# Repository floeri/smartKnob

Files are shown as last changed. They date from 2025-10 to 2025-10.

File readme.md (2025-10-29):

# Modified SmartKnob code for the MaTouch

This is a modified fork of https://gitee.com/coll45/super-dial-motor-knob-screen for the hardware of the MaTouch SmartKnob https://www.makerfabs.com/matouch-smartknob-assembled.html using the ESP-IDF

### Attention: 
the Arduino code in this repo is not yet modified for the MaTouch hardware, only the IDF code.

## Demo Mode:
currently there is a demo-mode implemented showing different grid sizes. The knob parameters for this are hardcoded in idf_code/main/ui/screens/ui_Screnn3.c

On the device you can reach the demo mode by selecting custom HID in the main menu

## TODOs
- translate chinese comments
- integrate tiny-usb midi library
- implement basic midi CC funktions to be able to use it as a midi controller
- create a flexible knob class that allows easy changes of the knob parameters
- restructure userinterface, get rid of unused code
- a lot of general refactoring

# Original README from the parent repo:

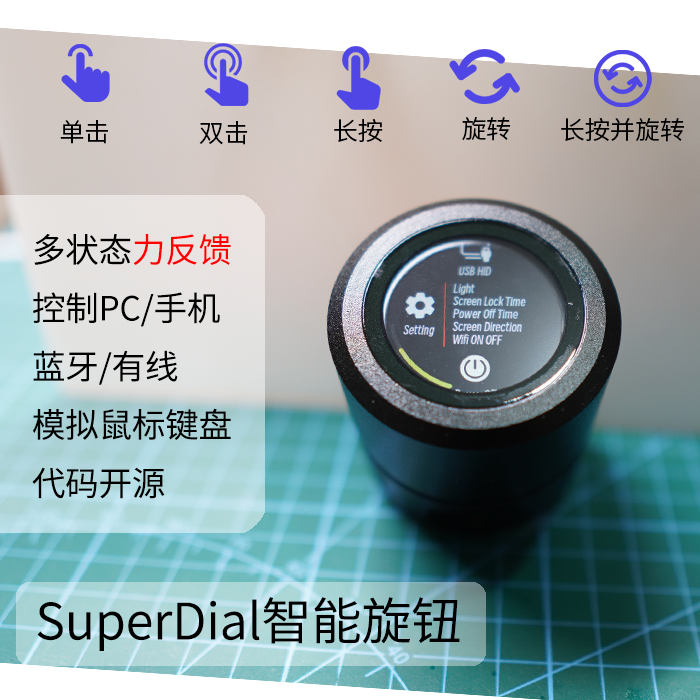
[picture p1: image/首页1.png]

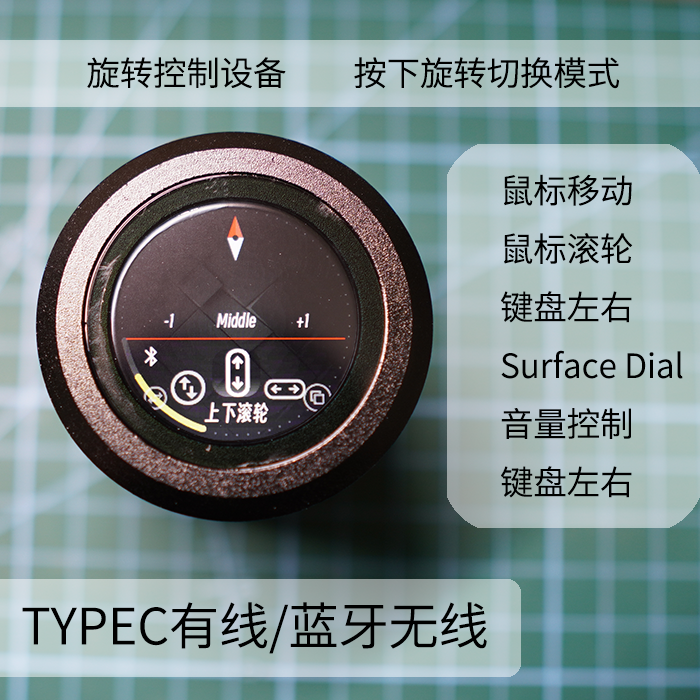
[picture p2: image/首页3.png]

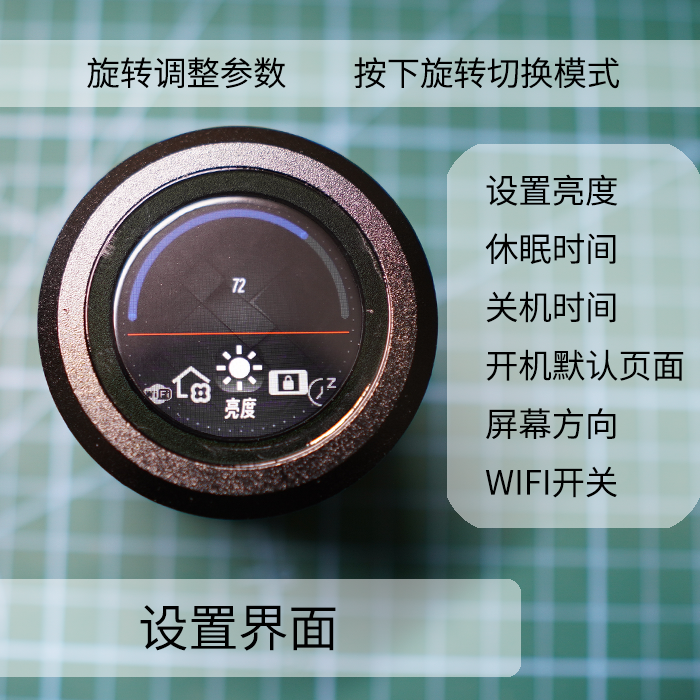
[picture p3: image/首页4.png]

# Super Dial 电机旋钮屏
##更新日志
### **重要更新2024/1/26:**
* **3205A电机已基本无货，需要改成3205B电机，修改内容如下**
  * 电机驱动板更改定位孔
  * 电机适配器修改为适配3205B
  * 电机转子套修改为适配3205B
  * 需要购买的螺丝变动具体查看3205B的bom表
### **重要更新2023/2/10:**

* **主控板V1更新为V2（打板 `不要打V1版本了）`，修复ip5306不稳定问题导致的电机转动时芯片重启、打开esp32wifi功能时供电不稳重启。 `删除USB引脚上的电容`（V1版本的C10、C11）让USB正常工作，原因是100nf电容太大了导致USB不能正常识别，去除电容就可以**
* **优化项：更换充电芯片使充电电流限制在400mA提高电池使用寿命，设计ups电路可实现USB和电池供电不间断切换，保证USB2.0也可以正常使用**
* **新的代码+固件也一并开源至Gitee**
* 硬件应该为最终版本，不再改动。代码会继续画饼（2024年注：电机坚持了一年才没货已经挺好了，所以硬件有小改动，换了几个螺丝孔位）

2022/10/10：原理图中usb5Vin 经过ip5036 再输出5v，会导致单usb供电的时候不稳定，会让电机控制或者蓝牙无法正常工作，暂时可以使用先usb和电池一起用。问题修复中，还没打板。
2022/11/11：发现程序之前mt6701磁编码器芯片用iic通信会有延迟现象，修改主控和电机驱动板的8p线走线，变成spi模式，磁编码器检测效果变好。不会出现力度突然大突然小的情况。（程序bin会后续修改，但是目前iic的程序可以在新版pcb上使用）

2022/11/24 修改bin文件，iic  -&gt; spi（老版本主控板不支持spi固件），替换力度控制功能为双击关机     spi固件已解决力度突然大突然小的问题，但是11.10之前版本的pcb不支持spi通信

## 1.项目介绍
灵感来源与国外的smart konb，制作初衷为制作一个桌面力反馈旋钮，可以与电脑进行交互。项目从最重要的电机入手，选择了量大便宜的3205电机（小米云台电机的库存货），在结构上实现上下等大，增加实用功能蓝牙hid（滚轮功能），可实现与surface dial一样的功能。演示视频[“SuperDial电机旋钮——力反馈、多功能”](https://www.bilibili.com/video/BV1cG411c7QS)
## 2.制作说明
硬件构成esp32s3-n16r8，屏幕为gc9a01，3个pcb，4个打印件，若干结构件。具体在附件——[附件gitee链接](https://gitee.com/coll45/super-dial-motor-knob-screen)

pcb：pcb打板都是2层板，1.6厚。`在立创下单参数都为默认`，只有颜色可以修改

1. 屏幕板，中间需要焊接铜柱（铜柱尖角对准线，可以用m2.5螺丝先固定后焊接，然后取出螺丝），8p0.8线通过铜柱往下连接到主控板（穿过电机中心，铜柱固定在打印件-适配器上）　<font color='red'> 下单屏幕板的时候注意备注： 不要半孔工艺</font>

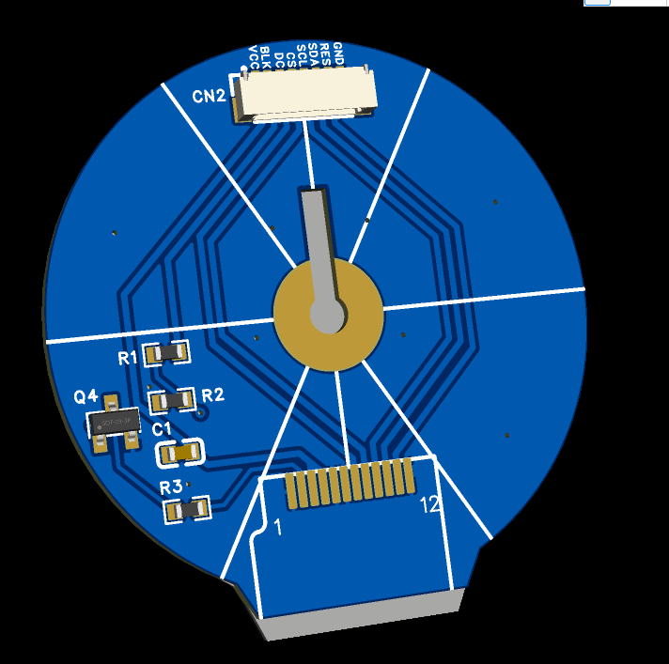
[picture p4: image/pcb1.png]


2.电机驱动板，含磁编码器。驱动芯片eg2133，磁编码器MT6701。穿过屏幕8p线后，驱动板通过螺丝固定在打印件-适配器上
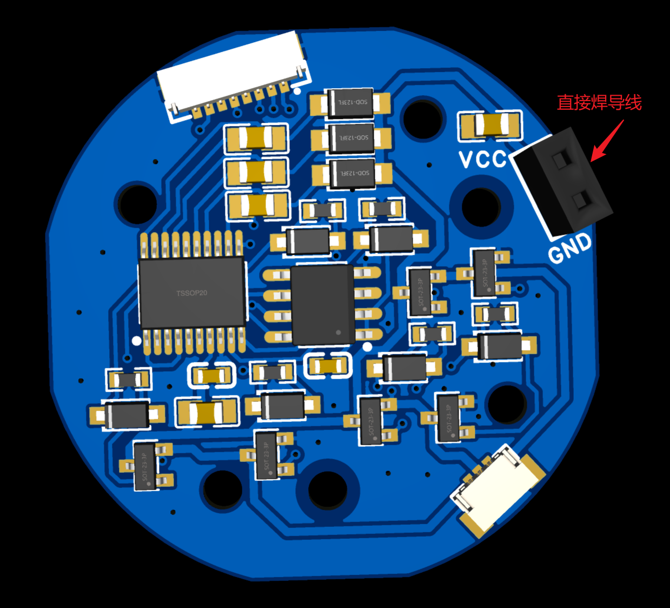
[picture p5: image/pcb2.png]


3.主控板,固定在底座上，背面朝上，电池放底部。typec一定需要USB3.0，5V1A以上，可实现充电、单独给旋钮供电（未来可以支持usb-hid）主控板上的2.54插针都不要焊接。
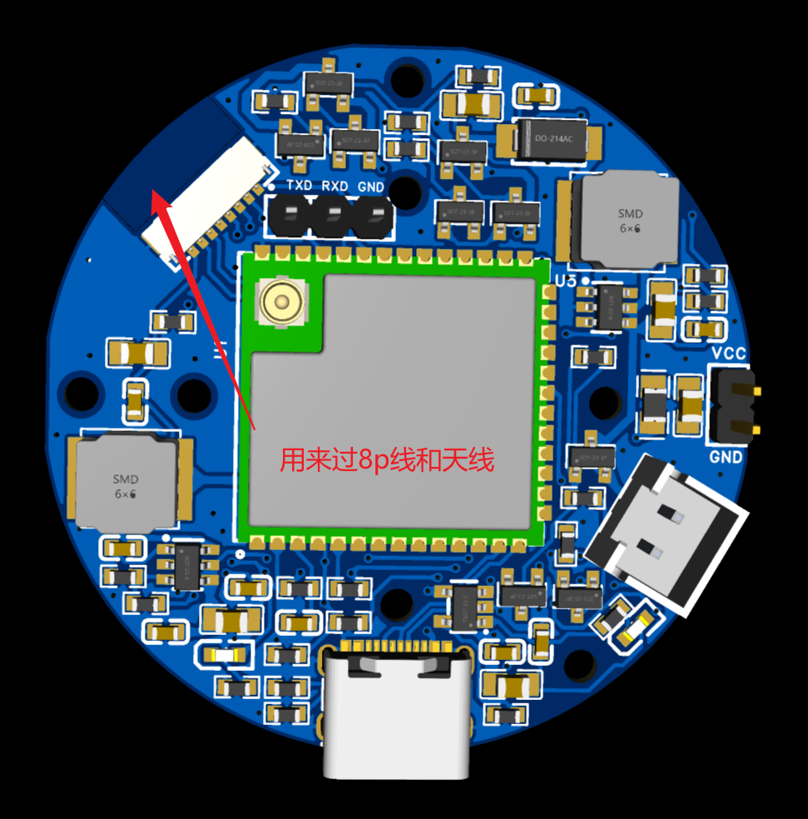
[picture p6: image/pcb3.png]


## 结构说明
打印件可以通过立创的三维猴打印，直接上传`3D打印和CNC模型-by虫二`文件夹内的step即可，一共四个打印件(有一个买电机会送),忽视壁厚小于0.8mm的警告，预计一套20-30。
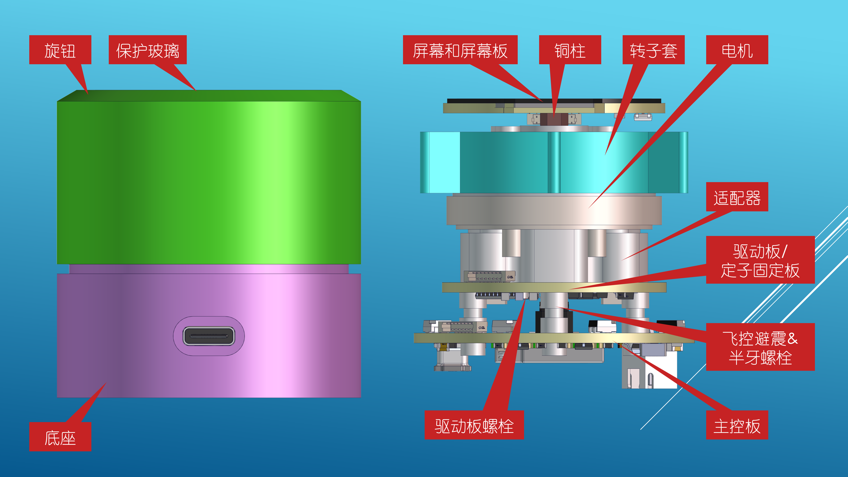
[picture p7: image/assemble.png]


## 组装说明
在文件夹中有`superdial装配教程.pdf`
## 代码烧录
USB烧录方法：打开附件文件夹内的`bin/flash_download_tool_3.9.2.exe` 选择esp32s3，loadmode改成USB，选择对应的bin文件，下载到自己电脑bin文件地址会变，需要重新选（idf_superdial.bin烧录到0x0位置），USB数据线连接，选择对应的com口。点start开始烧录。烧录完成后拔掉typec 再次插入就可以看见效果
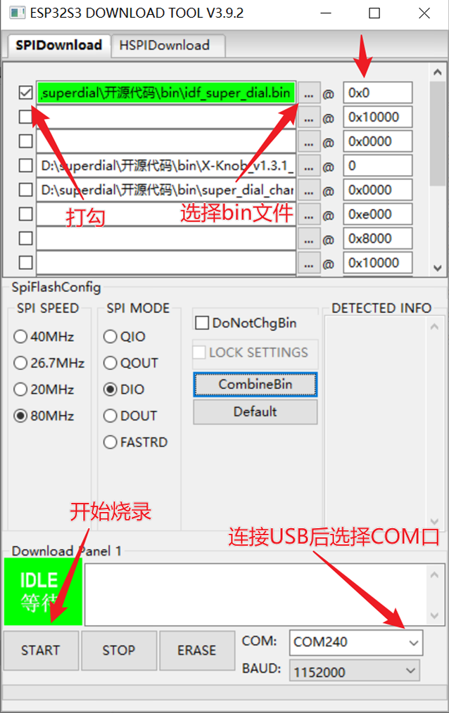
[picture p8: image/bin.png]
bin


代码第一次烧录会白屏很久(大概30秒)，因为在初始化spiffs文件系统，等初始化完成以后下次重启就不会白屏那么久了

## WIFI功能说明
旋钮有验证码机制，验证后可以实现wifi页面更换背景图片\自定义快捷键\自定义力反馈

选到设置界面-wifi-AP，长按启动热点，连接SuperDial-XXXXXX的wifi，打开浏览器访问192.168.4.1，选中wifi名称，填入密码和六位验证码
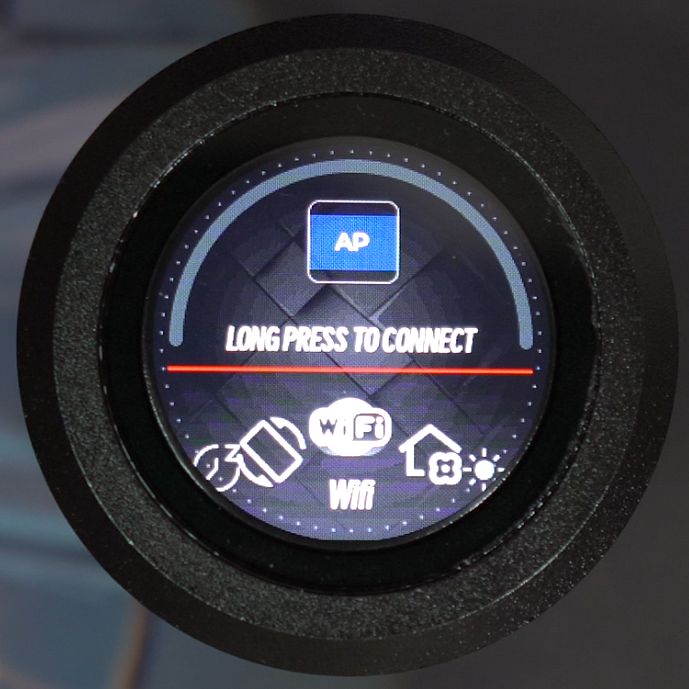
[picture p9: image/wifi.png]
wifi


验证码获取需要私聊作者QQ：674148718（请直接发消，不要加好友。或者发送邮件到674148718@qq.com）发送AP-wifi名称后六位，并发旋钮实物照片，证明是个人自制。作者会在一天之内回复六位验证码(拒绝提供验证码给闲鱼成品)

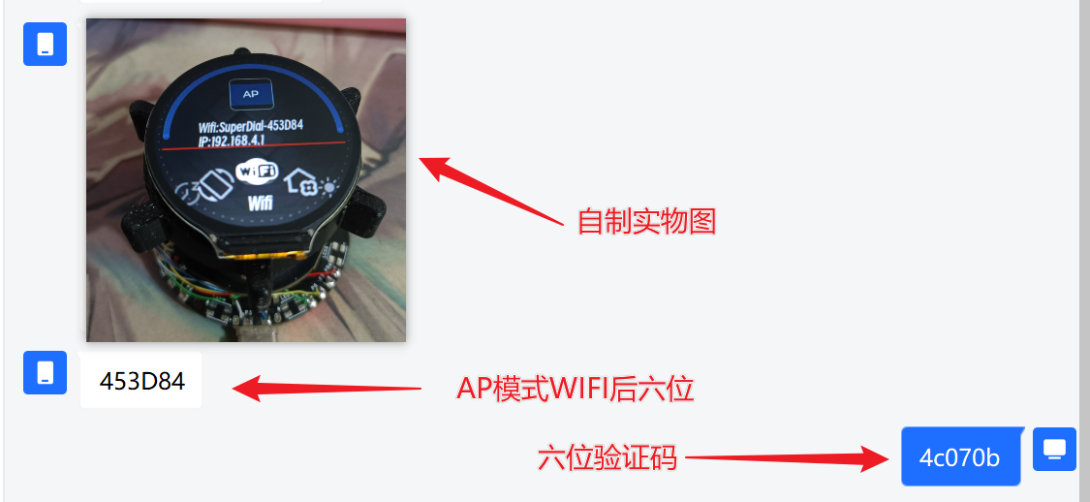
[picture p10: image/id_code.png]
id_code


填入验证码后，切换到STA模式，连接到自己的wifi，账号密码正常的情况会出现IP地址，与wifi同一局域网下，可以使用浏览器访问对应地址即可自定义快捷键和自定义背景图片。

常见问题：
1. 验证码填入后切换到STA模式还是显示账号、密码、验证码页面，说明验证码填写错误
2. 切换到STA模式连接wifi直接重启，STA模式只能连接2.4g频段wifi，5g频段不能使用，并且2.4g和5g共用的wifi也无法使用
## 源码
已经上传至gitee，主控芯片为：esp32s3-n16r8   开发环境为idf或arduino，代码在对应名称文件夹中

推荐用idf开发，只要安装idf5.0以上版本，即可直接编译运行源码。 不推荐的是arduino开发环境，需要自行修改lvgl配置文件，比较麻烦

idf的代码开放到wifi功能之前，可以实现力反馈控制、lvgl、USB-HID、蓝牙、设置界面等，可以用于学习/参考

## 未来计划（画饼）
项目初衷是做pc的外设所以打算都是开发pc功能。有能力大佬可以在开源的基础上自行修改。

1. ~~lvgl多级菜单实现多种界面效果（但是主要还是对pc设备win10系统的操作） ~~2023/2/10已实现
2. pc性能监视器
3. ~~wifi webserver实现图片修改 ~~  2024/6/1已实现
4. 实现midi控制
5. 屏保页面，动图显示（lottie动效）
6. 智能家居

## 沟通与交流
QQ群：816782369

## 感谢与引用
非常感谢虫二和立创的星火计划，让项目能够快速迭代落地 [fywbchong2](https://space.bilibili.com/438787726)

同时也感谢xknob作者mos，idf的代码更新参考了xknob功能 [xknob-项目链接](https://github.com/SmallPond/X-Knob)

还有非常感谢乐鑫开发者[老酸菜](https://github.com/lijunru-hub)提供的帮助，在idf开发过程中很多代码都是直接沿用[esp-iot-solution](https://github.com/espressif/esp-iot-solution/tree/master)中的示例

网页ui参考了开源作者：muyan的ESP32 UPS 12V [ESP32 UPS 12V 项目链接](https://gitee.com/muyan3000/esp32-ups-12-v)

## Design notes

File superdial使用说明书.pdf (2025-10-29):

默认 HID

设置界面

亮度：范围 1-100，转动到低时有电机软限位
息屏时间：不操作时屏幕熄灭；可选 30 秒、1 分钟、3 分钟、5 分钟、10 分钟、15 分钟、 从不息屏
关机时间：不操作自动关机时间；可选 1 分钟、3 分钟、5 分钟、10 分钟、15 分钟、30 分 钟、从不息屏
屏幕方向:屏幕显示方向；四个方向可调，每个方向间隔 90 度
Wifi：
STA 联网模式；长按联网后会访问对应的 wifi 热点，成功时会显示 IP 地址。在同一 wifi 热点内，打开浏览器访问 IP 地址会有设置网页
AP 热点模式；第一次使用需要进入到 AP 热点模式进行配网，wifi 名称“Superdial-xxxxxx”， 后六位是设备唯一 ID，在验证码获取时候需要填入后六位设备唯一 ID；验证码获取可以参 考项目 readme 里面说明，项目说明：https://gitee.com/coll45/super-dial-motor-knobscreen。选中对应 (https://gitee.com/coll45/super-dial-motor-knob-screen) wifi 名称，填入密码和验证码 默认首页：开机启动后默认打开的页面；可选首页，默认 HID，自定义 HID

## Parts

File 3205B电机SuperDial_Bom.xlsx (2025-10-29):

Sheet: 打印或CNC
SuperDial电机旋钮屏V2物料清单（打印件）
除旋钮外，均不需要添加支撑
旋钮同时支持CNC加工和3D打印
详见stl文件和step文件

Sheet: 其他辅料
SuperDial电机旋钮屏V2物料清单（其他辅料） |  |  |  | 链接
序号 | 数量 | 名称 | 备注
1 | 1 | 直径40mm厚度1mm玻璃 | 屏幕保护 | https://item.taobao.com/item.htm?abbucket=20&id=553695645065&ns=1&skuId=3728391490097
2 | 4 | M2*3杯头内六角螺丝 | 固定转子套 | https://detail.tmall.com/item.htm?id=43519715236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
3 | 3 | M2*5螺丝 | 固定主控和底座 | 可在上面链接配齐
4 | 1 | M2.5*5螺丝 | 辅助铜柱焊接 | 螺丝数量为用到的数量，实际上做一套旋钮只需要每个规格螺丝拍一件商品就行
5 | 6 | M2*12内六角半牙螺丝 | 穿过驱动板固定到电机/穿过主控板固定到适配器 | https://detail.tmall.com/item.htm?_u=p1sddf3sf272&id=687938827035&skuId=5075553231849
6 | 4 | M2*6.6MM飞控避震柱 | 套在半牙M2*12螺丝外 | https://item.taobao.com/item.htm?_u=p1sddf3s656f&id=648151872187&skuId=4864013272254
7 | 1 | M2.5*25六角铜柱双通 | 过屏幕线，得用（佰瑞特紧固件企业店）的铜柱 | https://item.taobao.com/item.htm?_u=p1sddf3s5d27&id=20345879255&skuId=5173597151816
8 | 1 | 502胶水 | 固定屏幕玻璃到打印件上
9 | 1 | 间距0.8mm 8P 32AWG单头线 | 屏幕线，长度20cm | https://item.taobao.com/item.htm?_u=p1sddf3sefb6&id=582653807364&skuId=4510259621478
10 | 1 | 间距0.8mm 8P 32AWG双头同向线 | 连接驱动和主控，越短越好（可定制） | 上面链接8p双头同向10cm长度的也可以用，就是要稍微理一下线
11 | 1 | 3205电机B款 无限位 | 在45菌店铺买无限位款可以备注（旋钮）会送对应适配器 | https://item.taobao.com/item.htm?id=734772197083&skuId=5254200511031
12 | 1 | 2P杜邦线适量长度 | 连接主控和驱动，导线自己裁剪合适长度
13 | 1 | 602535锂电池 600mAh | 可小不可大；不带插头、xh2.54和ph2.0均可（线长50mm） | https://item.taobao.com/item.htm?_u=p1sddf3s11e1&id=619805501404&skuId=4627654124871
14 | 1 | 0.15mm双面胶适量 | 固定屏幕，旋钮套和外壳固定
15 | 1 | FPC软天线IPEX 1代 | A款FPC 5DB 37*10mm 线总长6cm IPEX 1代 | https://item.taobao.com/item.htm?_u=p1sddf3s7e17&id=586127342811&skuId=4017577965337
16 | 1 | 直径54mm左右防滑硅胶垫 | 贴在底座底面（定制） | 不影响功能，可不买
17 | 1 | 1.28寸TFT液晶显示屏GC9A01驱动 | 标准焊接款（不带触摸） | https://item.taobao.com/item.htm?_u=q1sddf3sfeb4&id=674420369037&skuId=5027778451275
18 | 1 | ESP32S3-N16R8 | 立创原理图上用的是N8是错的，需要买N16R8 | https://item.taobao.com/item.htm?abbucket=16&id=676604026231&ns=1&skuId=5035236575059

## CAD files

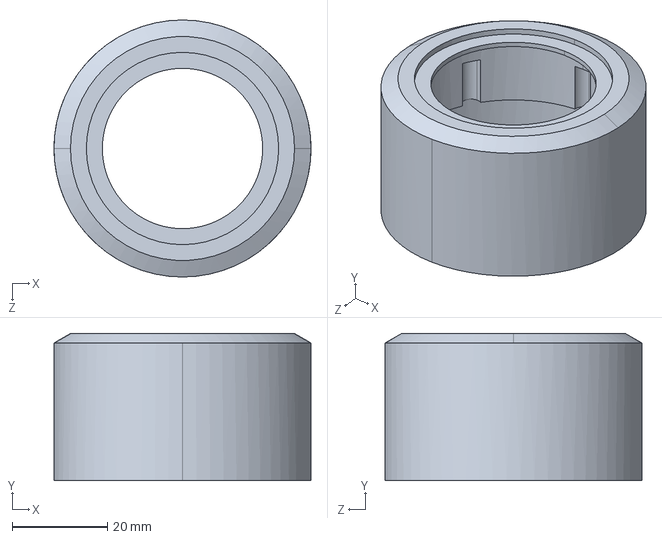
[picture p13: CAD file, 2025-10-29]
3D打印和CNC模型-by虫二/旋钮上盖.STEP
54.0 x 30.9 x 54.0 mm

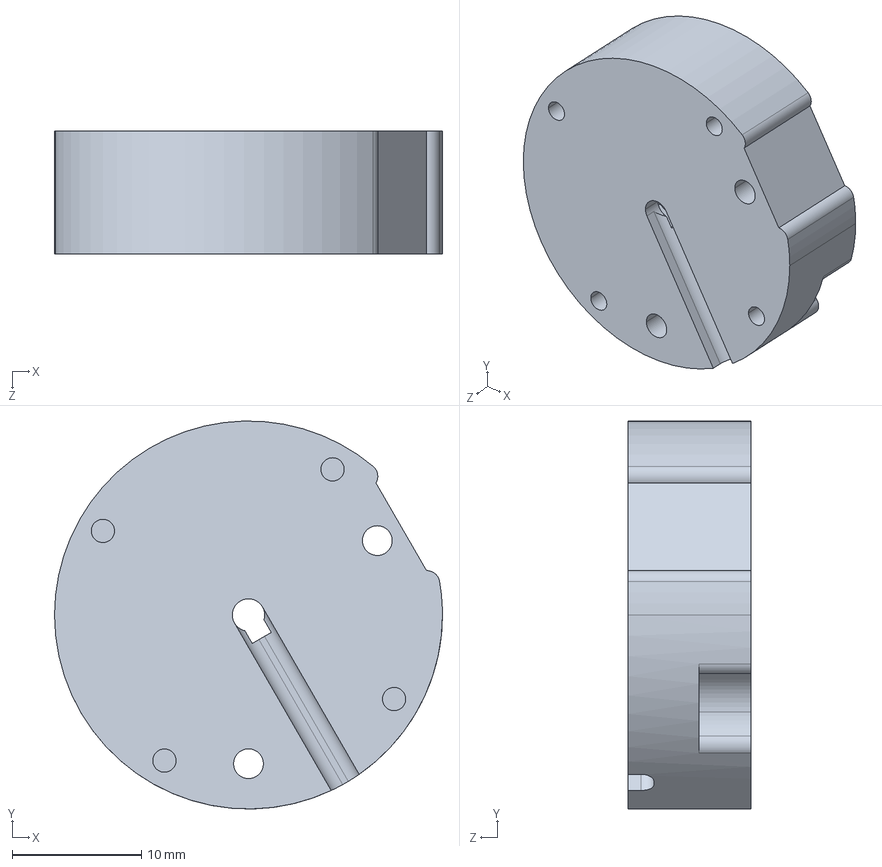
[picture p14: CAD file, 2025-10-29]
3D打印和CNC模型-by虫二/3205b适配器.STEP
30.0 x 30.0 x 9.50 mm

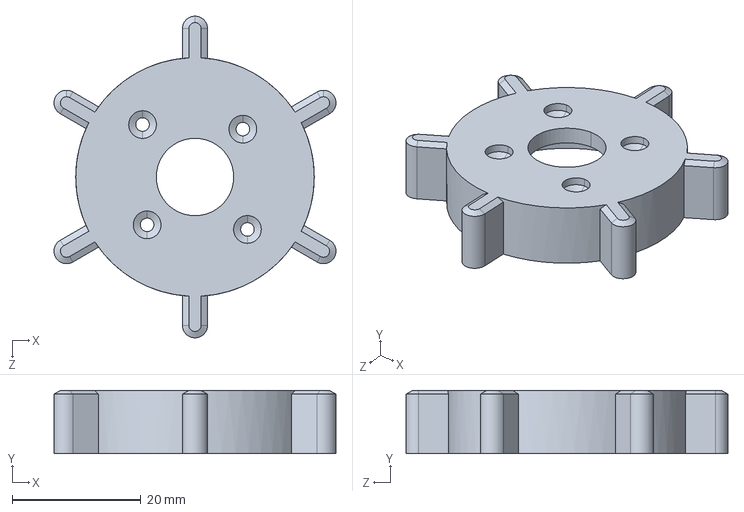
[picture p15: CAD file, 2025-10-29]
3D打印和CNC模型-by虫二/3205b电机转子套.STEP
43.7 x 9.80 x 49.9 mm

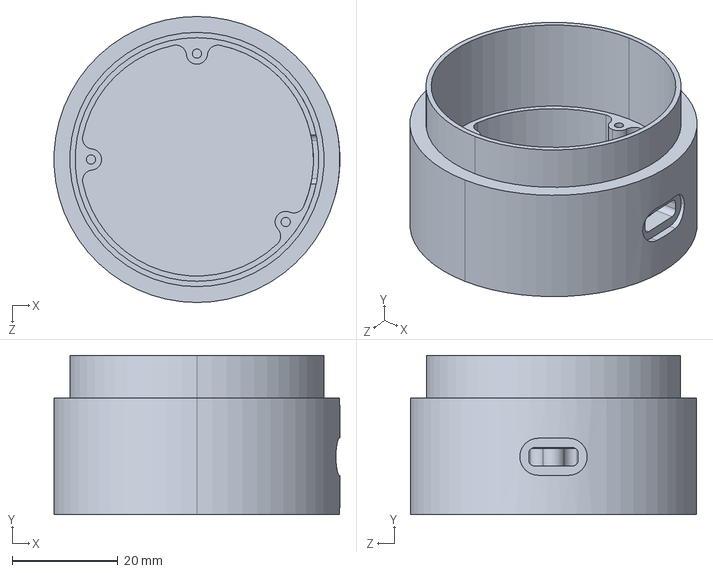
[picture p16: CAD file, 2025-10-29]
3D打印和CNC模型-by虫二/旋钮底座.STEP
53.9 x 30.1 x 54.0 mm

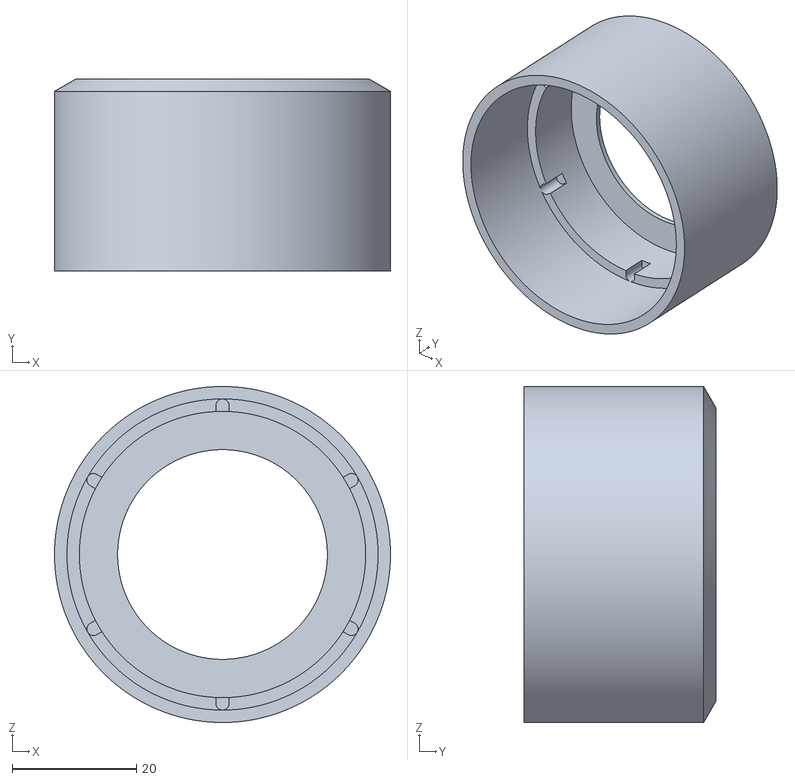
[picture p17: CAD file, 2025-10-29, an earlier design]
3D打印和CNC模型-by虫二/旧版本3205A电机结构模型_仅供参考/01.旋钮.STL
54.0 x 30.9 x 54.0

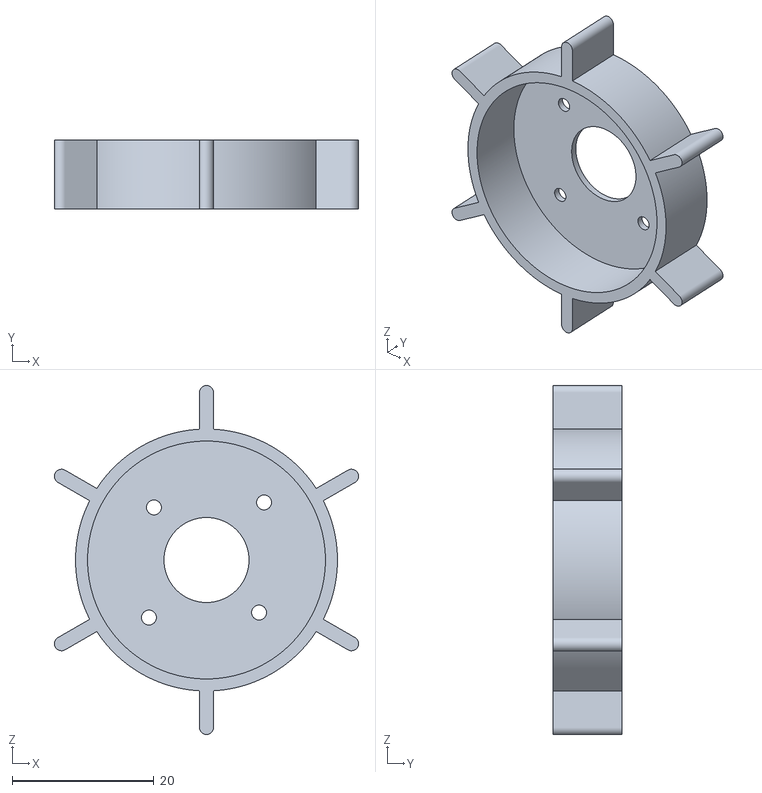
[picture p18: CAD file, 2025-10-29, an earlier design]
3D打印和CNC模型-by虫二/旧版本3205A电机结构模型_仅供参考/04.转子套.STL
43.0 x 9.80 x 49.3

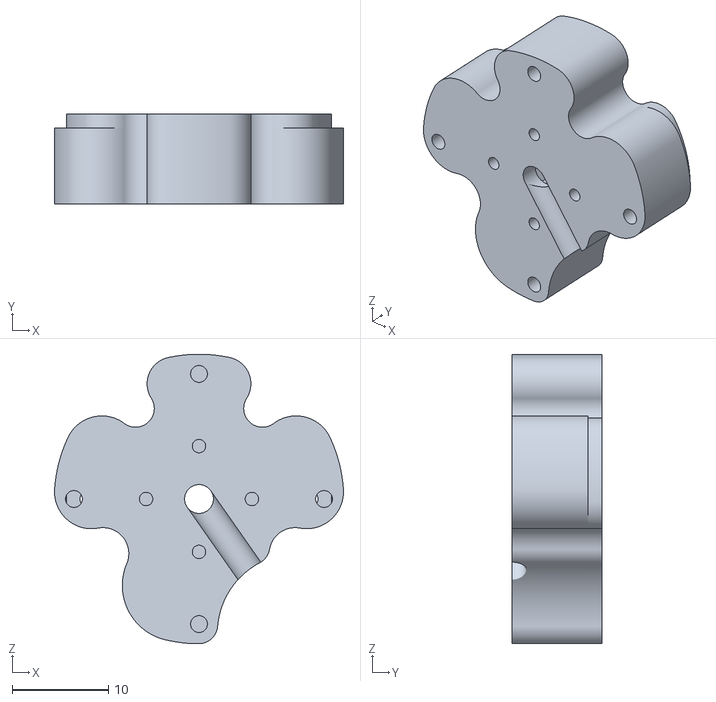
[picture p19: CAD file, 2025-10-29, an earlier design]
3D打印和CNC模型-by虫二/旧版本3205A电机结构模型_仅供参考/03.适配器.STL
30.0 x 9.40 x 30.1

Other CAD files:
3D打印和CNC模型-by虫二/旧版本3205A电机结构模型_仅供参考/02.底座.STL
3D打印和CNC模型-by虫二/旧版本3205A电机结构模型_仅供参考/01.旋钮CNC用.STEP

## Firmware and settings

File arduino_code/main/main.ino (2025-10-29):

#include "motor_task.h"
#include "display_task.h"
#include "interface.h"
// #include <SimpleFOC.h>
// #include "i2c.h"





TaskHandle_t xTask1;
TaskHandle_t xTask2;
TaskHandle_t xTask3;
//static MotorTask motor_task = MotorTask();
void setup() {
  // monitoring port
  Serial.begin(115200);
  delay(100);
  ffat_init();
  if (!EEPROM.begin(1000)) {
    Serial.println("Failed to initialise EEPROM");
    Serial.println("Restarting...");
    delay(1000);
    ESP.restart();
  }

  pthread_mutex_init(&lvgl_mutex, NULL);
  /* 创建队列，其大小可包含5个元素Data */
  queue_ = xQueueCreate(5, sizeof(Command));
  assert(queue_ != NULL);
  knob_state_queue_ = xQueueCreate(1, sizeof(KnobState));
  assert(knob_state_queue_ != NULL);
  xTaskCreatePinnedToCore(
    interface_run,
    "interface_run",
    8192,
    NULL,
    2,
    &xTask3,
    1);
  xTaskCreatePinnedToCore(
    motor_run,
    "motor_task", /* 任务名称. */
    8192,         /* 任务的堆栈大小 */
    NULL,         /* 任务的参数 */
    1,            /* 任务的优先级 */
    &xTask1,      /* 跟踪创建的任务的任务句柄 */
    1);           /* pin任务到核心0 */

  display_init();
  xTaskCreatePinnedToCore(
    display_run,
    "display_run",
    20000,
    NULL,
    0,
    &xTask2,
    0);


  vTaskDelete(NULL);
}

void loop() {
  // lv_timer_handler(); /* let the GUI do its work */
  // vTaskDelay(0);
  // motor_run();
}

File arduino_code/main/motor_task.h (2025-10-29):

#ifndef __MOTOR_TASK_H__
#define __MOTOR_TASK_H__
#include <Arduino.h>
#include <SimpleFOC.h>
#include "Wire.h"
#include <SPI.h>
#include "EEPROM.h"

#define MO1 GPIO_NUM_17
#define MO2 GPIO_NUM_16
#define MO3 GPIO_NUM_15
static const int spiClk = 1000000; // 400KHz
SPIClass* hspi = NULL;
#define MT6701_SDA 1
#define MT6701_SCL 2
#define MT6701_SS 42
uint8_t sleep_flag = 0;
xQueueHandle knob_state_queue_;
xQueueHandle queue_;
struct KnobConfig {
  int32_t num_positions;
  int32_t position;
  float position_width_radians;
  float detent_strength_unit;
  float endstop_strength_unit;
  float snap_point;
};
struct KnobState {
  int32_t current_position;
  float sub_position_unit;
  KnobConfig config;
};
enum class CommandType {
  CONFIG,
  HAPTIC,
};
struct HapticData {
  bool press;
};
struct Command {
  CommandType command_type;
  union CommandData {
    KnobConfig config;
    HapticData haptic;
  };
  CommandData data;
};
void publish(const KnobState& state);
void calibrate();
template<typename T> T CLAMP(const T& value, const T& low, const T& high) {
  return value < low ? low : (value > high ? high : value);
}
static const float DEAD_ZONE_DETENT_PERCENT = 0.2;
static const float DEAD_ZONE_RAD = 1 * _PI / 180;

static const float IDLE_VELOCITY_EWMA_ALPHA = 0.001;
static const float IDLE_VELOCITY_RAD_PER_SEC = 0.05;
static const uint32_t IDLE_CORRECTION_DELAY_MILLIS = 500;
static const float IDLE_CORRECTION_MAX_ANGLE_RAD = 5 * PI / 180;
static const float IDLE_CORRECTION_RATE_ALPHA = 0.0005;

//目标变量
float readMySensorCallback() {
    hspi->beginTransaction(SPISettings(spiClk, MSBFIRST, SPI_MODE0));
    digitalWrite(hspi->pinSS(), LOW); //pull SS slow to prep other end for transfer
    uint16_t ag = hspi->transfer16(0);
    digitalWrite(hspi->pinSS(), HIGH); //pull ss high to signify end of data transfer
    hspi->endTransaction();
    ag = ag >> 2;
    float rad = (float)ag * 2 * PI / 16384;
    if (rad < 0) {
        rad += 2 * PI;
    }
  return rad;
}
void initMySensorCallback() {
  // do the init
    hspi = new SPIClass(HSPI);
    hspi->begin(MT6701_SCL, MT6701_SDA, -1, MT6701_SS); //SCLK, MISO, MOSI, SS
    pinMode(hspi->pinSS(), OUTPUT); //HSPI SS
}
BLDCMotor motor = BLDCMotor(7);
BLDCDriver3PWM driver = BLDCDriver3PWM(MO1, MO2, MO3);
GenericSensor sensor = GenericSensor(readMySensorCallback, initMySensorCallback);
float idle_check_velocity_ewma = 0;
uint32_t last_idle_start = 0;
uint32_t last_debug = 0;
float target_velocity = 0;
float current_detent_center, last_angle;
uint32_t last_publish = 0;

KnobConfig config = {
  .num_positions = 0,
  .position = 0,
  .position_width_radians = 1 * _PI / 180,
  .detent_strength_unit = 1,
  .endstop_strength_unit = 1,
  .snap_point = 1.1,
};
void init_foc()
{
  sensor.init();
  //连接motor对象与传感器对象
  motor.linkSensor(&sensor);
  // PWM 频率 [Hz]
  driver.pwm_frequency = 50000;
  //供电电压设置 [V]

  driver.voltage_power_supply = 5;
  driver.init();
  motor.linkDriver(&driver);
  //FOC模型选择
  motor.foc_modulation = FOCModulationType::SpaceVectorPWM;
  //运动控制模式设置
  motor.controller = MotionControlType::torque;
  //速度PI环设置
  motor.PID_velocity.P = 2;
  motor.PID_velocity.I = 0;
  motor.PID_velocity.D = 0.08;
  motor.PID_velocity.output_ramp = 10000;
  motor.PID_velocity.limit = 10;
  //最大电机限制电机
  motor.voltage_limit = 5;
  //速度低通滤波时间常数
  motor.LPF_velocity.Tf = 0.01;
  //设置最大速度限制
  motor.velocity_limit = 40;

  motor.useMonitoring(Serial);
  //初始化电机
  motor.init();
  //初始化 FOC 
  // calibrate();
 if(isnan(EEPROM.readFloat(0))||EEPROM.readFloat(0)>=100)
  {
      if(motor.initFOC())
      {
        Serial.println(motor.pole_pairs);
        motor.pole_pairs = 7;
      }
  }
  else
  {
    float zero_electric_offset = EEPROM.readFloat(0);
    motor.pole_pairs = 7;
    Direction foc_direction = Direction::CW;
    motor.initFOC(zero_electric_offset, foc_direction);
  }

  //   calibrate();
  motor.monitor_downsample = 0;  // disable monitor at first - optional
  Serial.println(F("Motor ready."));
  Serial.println(F("Set the target velocity using serial terminal:"));

  current_detent_center = motor.shaft_angle;
}
void motor_task_init() {

    init_foc();
  // Update derivative factor of torque controller based on detent width.
  // If the D factor is large on coarse detents, the motor ends up making noise because the P&D factors amplify the noise from the sensor.
  // This is a piecewise linear function so that fine detents (small width) get a higher D factor and coarse detents get a small D factor.
  // Fine detents need a nonzero D factor to artificially create "clicks" each time a new value is reached (the P factor is small
  // for fine detents due to the smaller angular errors, and the existing P factor doesn't work well for very small angle changes (easy to
  // get runaway due to sensor noise & lag)).
  // TODO: consider eliminating this D factor entirely and just "play" a hardcoded haptic "click" (e.g. a quick burst of torque in each
  // direction) whenever the position changes when the detent width is too small for the P factor to work well.
  const float derivative_lower_strength = config.detent_strength_unit * 0.08;
  const float derivative_upper_strength = config.detent_strength_unit * 0.02;
  const float derivative_position_width_lower = radians(3);
  const float derivative_position_width_upper = radians(8);
  const float raw = derivative_lower_strength + (derivative_upper_strength - derivative_lower_strength) / (derivative_position_width_upper - derivative_position_width_lower) * (config.position_width_radians - derivative_position_width_lower);
  motor.PID_velocity.D = CLAMP(
                           raw,
                           min(derivative_lower_strength, derivative_upper_strength),
                           max(derivative_lower_strength, derivative_upper_strength));
}
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
